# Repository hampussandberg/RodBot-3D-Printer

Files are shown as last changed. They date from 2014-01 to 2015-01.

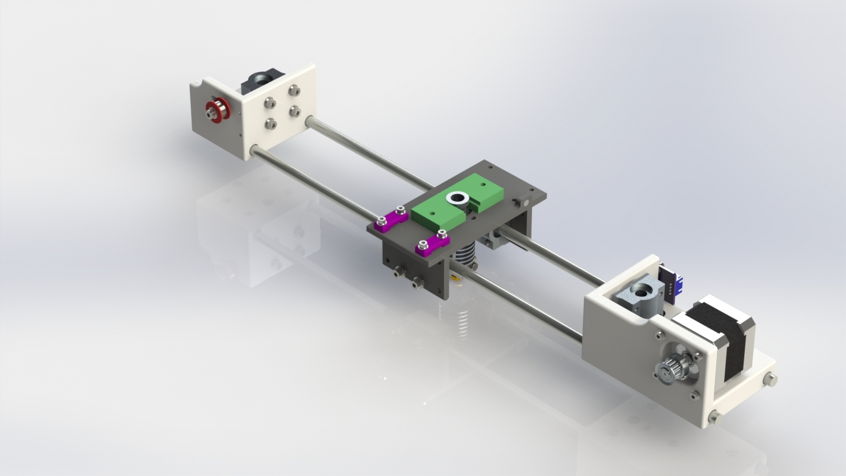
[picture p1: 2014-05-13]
Renderings - Images/X-Assembly Rev 2.JPG

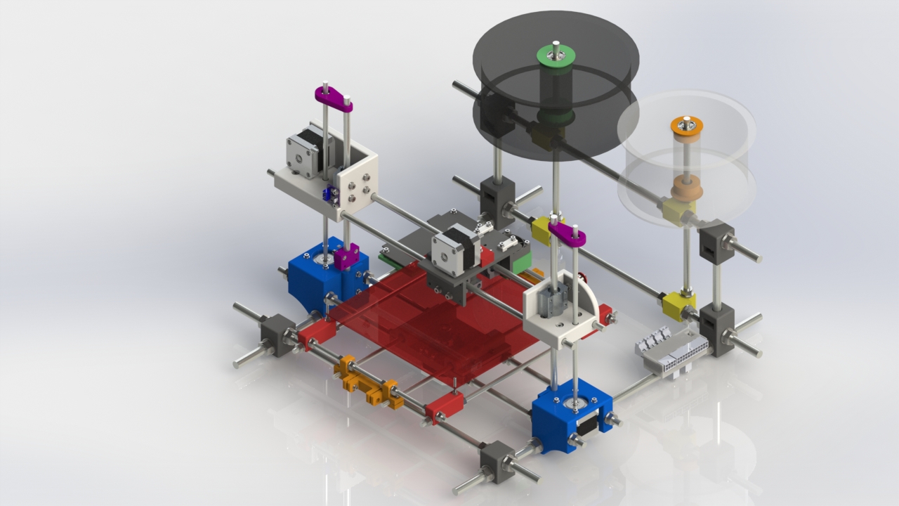
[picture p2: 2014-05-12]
Renderings - Images/Assembly.JPG

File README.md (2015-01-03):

##RodBot - 3D Printer  

This project started out as a small upgrade to a kit 3D printer I bought but ended up as a complete printer.  

It is designed around a frame of M10 threaded rods for stability, which is where the name come from as well. All plastic parts are printable and are made to be sturdy for stability.  

The weakest link I found in the kit printer I started out with was that many printed parts where mounted together to form a bigger part. I tried to avoid this by making the parts as big as necessary and only mounting hardware like rods and bearing blocks. This will of course mean more material is needed and the total weight of the printed parts is around 900 grams.  

The X-carriage was designed to fit a [Greg's Wade reloaded](http://www.thingiverse.com/thing:18379) or my remix of [Minimalistic Mk7 replacement](http://www.thingiverse.com/thing:251112)  
It's probably possible to use other extruders using the 50 mm hole distance as well.  

Some of the parts needed:  
* M10 threaded rods + nuts and washers  
* M8 threaded rods + nuts and washers  
* M6 threaded rods + nuts and washers  
* 8 mm Smooth rods  
* SC8UU bearing blocks  
* RepRap PCB Heatbed, I'm using [this one](http://reprap.me/heatbed/mk2-231.html)  

**Note:** Some parts might need to be rotated in order to print them.  

The frame blocks are designed to work with this [Heavy duty Vibration damper](http://www.thingiverse.com/thing:94279 )  

I have made a 3D PDF of the printer available for [download](https://github.com/hampussandberg/RodBot-3D-Printer/raw/master/Renderings%20-%20Images/RodBot%20Assembly%20Rev%203.PDF)  

##Updates:  
**2015-01-03:** Some changes have been made since the last update. The biggest are:  
- New heatbed: [Helios Heat Bed kit](http://www.panucatt.com/product_p/hbp200.htm)  
- New extruder: [Bulldog XL Extruder](http://www.reprapdiscount.com/mechanics/64-bulldog-xl-extruder.html)  
- Changed Z-axis threaded rods to [trapezoidal lead screw](http://www.ebay.com/itm/TR8x1-5Dx180mm-1-5mm-Pitch-Trapezoidal-Acme-Ballscrew-Leadscrew-Fine-Pitch-/221553098138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)  
- Adjustable belt tensioner for the X-axis  
All these changes has made the printer better and more importantly it seems like it's more reliable. All the new files are available on the [Github page](https://github.com/hampussandberg/RodBot-3D-Printer).  

**2014-05-30:** The Y-axis is now modified to use 8 mm smooth rods so that those are the only rods used for the whole printer and SC8UU are used everywhere. I also modifided the design of the Y-motor mount to be able to print it flat (prints faster) and tried to make it more robust. I recommend printing the Y-motor mount at 100% infill. The new parts are:  
- Y Motor Mount Rev 2  
- Y Smooth Rod Ends - Rev 2.1  
- Y Belt Holder Rev 2  

**2014-05-13:** The Marlin configuration I'm using with the RAMPS controller is available on [Github](https://github.com/hampussandberg/RodBot-Marlin-Ramps). I've also moved old compenent no longer used on the newest version of RodBot to an archive folder [here](https://github.com/hampussandberg/RodBot-3D-Printer/tree/master/Archive).    

**2014-05-12:** Modified the Y ends to have a easier and more robust clamp for the belt. It is now easier to adjust the tension as it's just a matter of turning to screws. This also removes the problem I had with the plastic holding the belt cracking. The new parts are:  
- Y Smooth Rod Ends - Rev 2  
- Y Belt Holder  
Hardware needed:  
- 2 pcs M3x25mm or longer  
- 2 pcs M3x16mm  
- 4 pcs M3 Lock nut  
- 2 pcs M3 nut  
- 8 pcs M3 washer  
Some photos of the assembly: [Photo 1](https://raw.githubusercontent.com/hampussandberg/RodBot/master/Renderings%20-%20Images/Photo%202014-05-12%2023%2004%2008.jpg), [Photo 2](https://raw.githubusercontent.com/hampussandberg/RodBot/master/Renderings%20-%20Images/Photo%202014-05-12%2023%2003%2046.jpg), [Photo 3](https://raw.githubusercontent.com/hampussandberg/RodBot/master/Renderings%20-%20Images/Photo%202014-05-12%2023%2003%2052.jpg).  

**2014-05-08:** All files are available on [GitHub](https://github.com/hampussandberg/RodBot-3D-Printer) along with some development and some old files as well.  

**2014-04-30:** I recently replaced my J-Head hotend with an [E3D hotend](http://e3d-online.com/) but I needed to widen the x assembly by 5 mm in order to fit it. The new parts for the wider x-assembly are:  
- X Carriage Rev 3  
- X-End Idler Clamp Rev 2  
- X-End Idler Rev 2  
- X-End Motor Clamp Rev 2  
- X-End Motor Rev 2  
To secure the E3D Hotend I'm using [this mount from dmarett](http://www.thingiverse.com/thing:220811). See the pictures I've taken for more details.

**2014-03-29:** The fan mount I designed didn't work very well so I have now replaced it with [this](http://www.thingiverse.com/thing:283862), which is a remix of [this one](http://www.thingiverse.com/thing:30721) but with a slightly modified mount to fit on the two screws for the belt holders.

##License
<br />This work is licensed under a <a rel="license" href="http://creativecommons.org/licenses/by-sa/4.0/">Creative Commons Attribution-ShareAlike 4.0 International License</a>.

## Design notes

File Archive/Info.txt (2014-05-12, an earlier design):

Upgraded version of Portabee

Some parts might need to be rotated so they are printed correctly.  

Works nicely with these vibration dampers http://www.thingiverse.com/thing:94279  

**UPDATE Dec 12 - 2013**  
Working on the x-assembly right now with a new extruder mount which hopefully will be more stable than the current one. I've also designed some new end stops based on A1301 hall sensors, just waiting for the PCB's to arrive so I can start using them. For the x-assembly I've been using SC8UU linear bearings found on eBay. They seem to be quite sturdy! I will update more once I receive some more bearings so that I can start assembling the x-assembly.  
I've exported a 3D-PDF available in the download section or here: http://www.thingiverse.com/download:377081  

**UPDATE Nov 13 - 2013**   
I have now printed and assembled a version which works. Some small changes has been made to make all the parts more robust so any real pictures of the machine might differ a bit from the STL-models. Works extremely well and feels very strong which was the main reason I started with this upgrade. As it stands now only the X-assembly is still the original from Portabee but I intend on upgrading it as well which will make the whole machine "new"!  

I have now uploaded all the new parts that I use. Additional hardware is required:  
- M6 threaded rods and 6mm smooth rods for Y-assembly + nuts and washers  
- M10 threaded rods for the main frame + nuts and washers  
- Mostly M3 hex screws of various length (10, 12, 16, + some more)  
- M8 threaded rods to mount the Y-assembly on  

Total build area is now 175x150x150mm (X Y Z).  
I will update with a complete list when I have more time!  

**UPDATE Oct 2 - 2013**  
After designing the frame i realized how unstable the printer was in it self so I started working on a new base which is part of the frame (the blue pieces in the rendering). I noticed the y-assembly had some cracks in the parts so I designed a new single-block version and I also replaced the standard heatbed with a reprap one to get a bigger build area. (Basically all parts under the red heatbed in the rendering)  

**NOTE:**  
I'm still designing the parts and haven't printed them yet but here are some features the upgraded printer will have:  
- Bigger build area (200x200)  
- More stable y-assembly  
- Hall sensor endstops using A1301 for easier adjustment  
- Variable width for other types of build platform. Change the length of the rods for your needs  
- M8 threaded rods for y-assembly instead of M6  
- Electronics holder with cover (green part on the left side in rendering)  
- Probably more stuff once I'm done with the above  

**Feedback and/or requests are gladly received!**  

Parts with name OLD_nnn are parts from the old design where the original printer parts were placed in a holder on the metal frame.

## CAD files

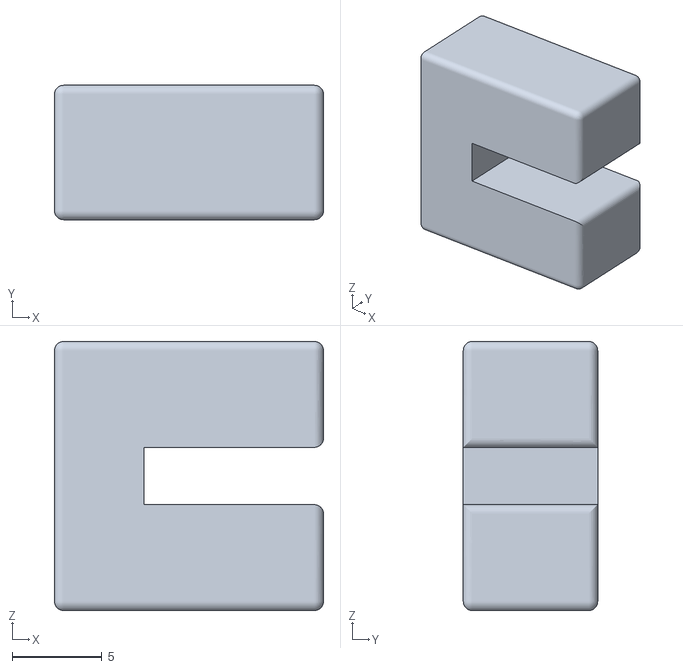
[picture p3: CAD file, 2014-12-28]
Accessories/Build Plate Holder/Clamp - 3.2mm.STL
15.0 x 7.50 x 15.0

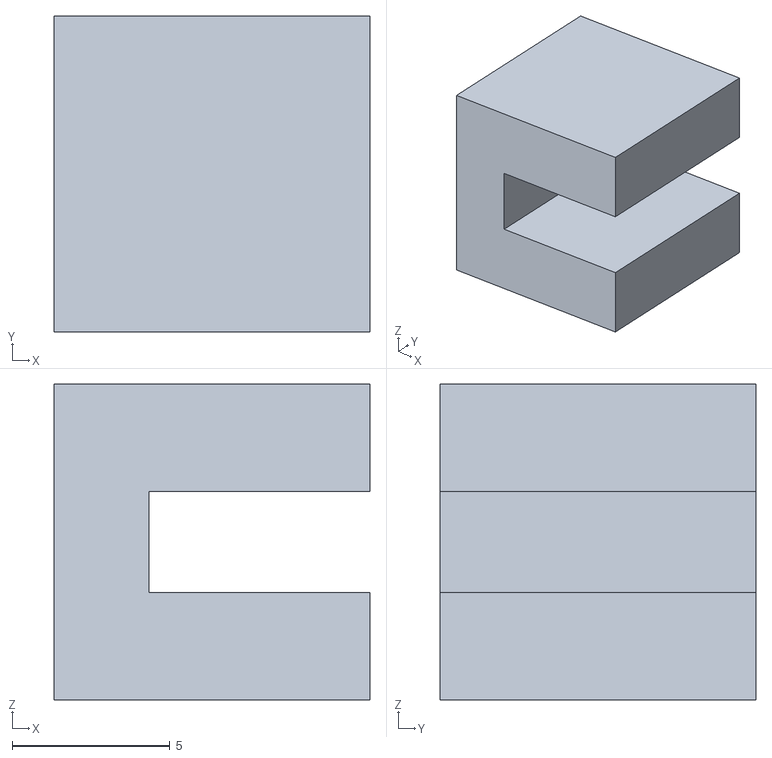
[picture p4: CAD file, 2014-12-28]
Accessories/Clamp.STL
10.0 x 10.0 x 10.0

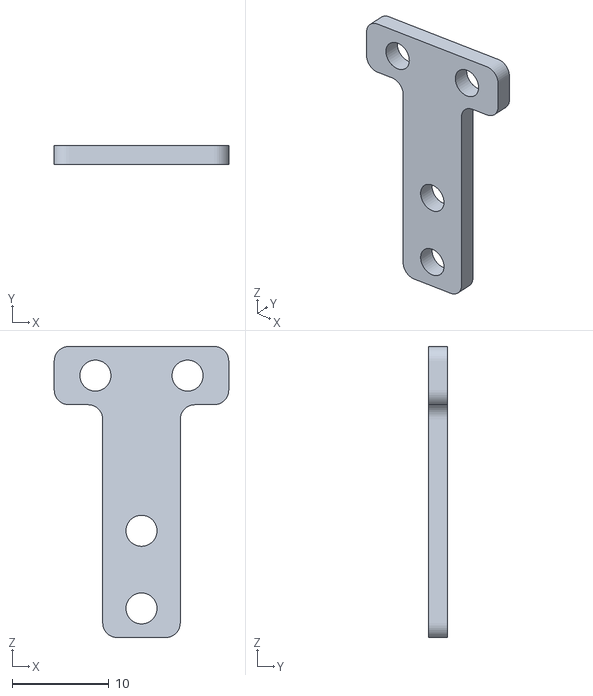
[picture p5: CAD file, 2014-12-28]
Accessories/Servo Holder/Switch Servo Horn Extension.STL
18.0 x 2.00 x 30.0

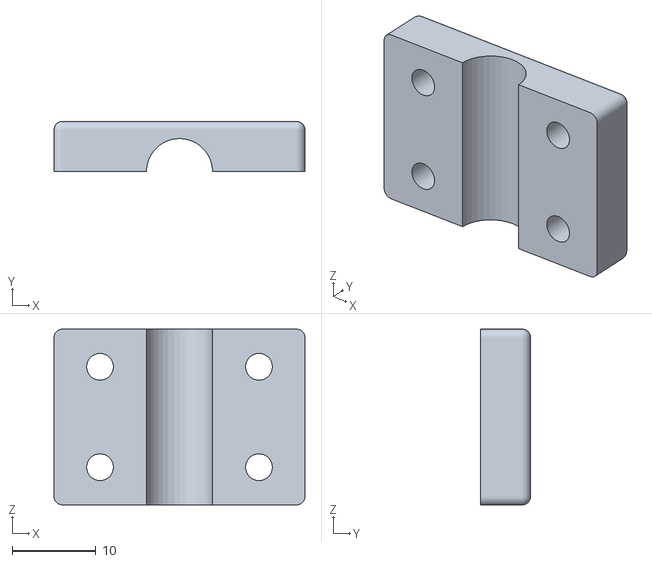
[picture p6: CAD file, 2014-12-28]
Z Endstop Holder.STL
30.0 x 6.00 x 21.0

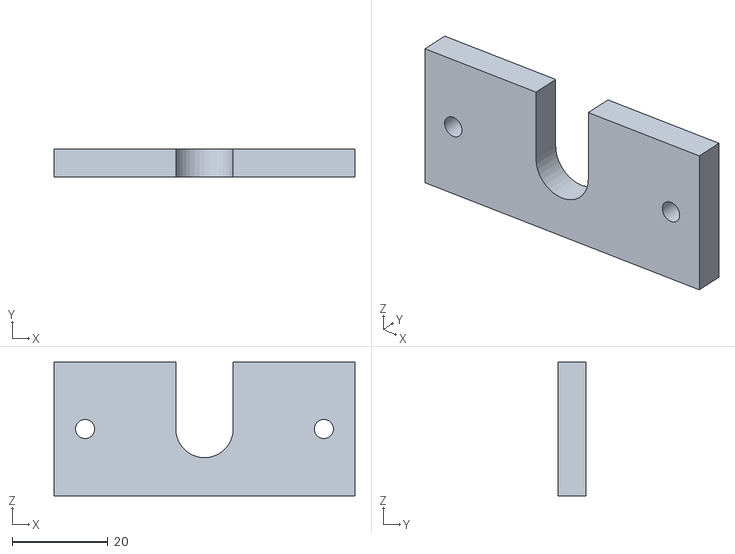
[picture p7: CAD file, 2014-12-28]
Accessories/E3D-v6 Mounting Plate.STL
63.0 x 5.80 x 28.0

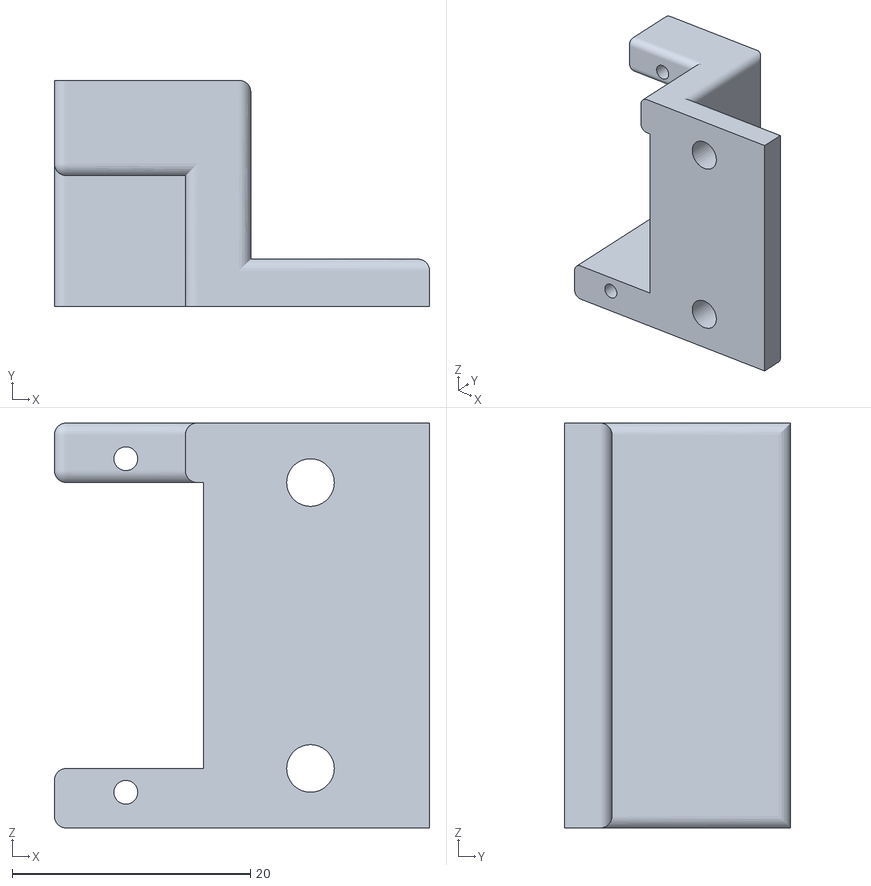
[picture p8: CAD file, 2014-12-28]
Accessories/Servo Holder/Servo Holder.STL
31.5 x 19.0 x 34.0

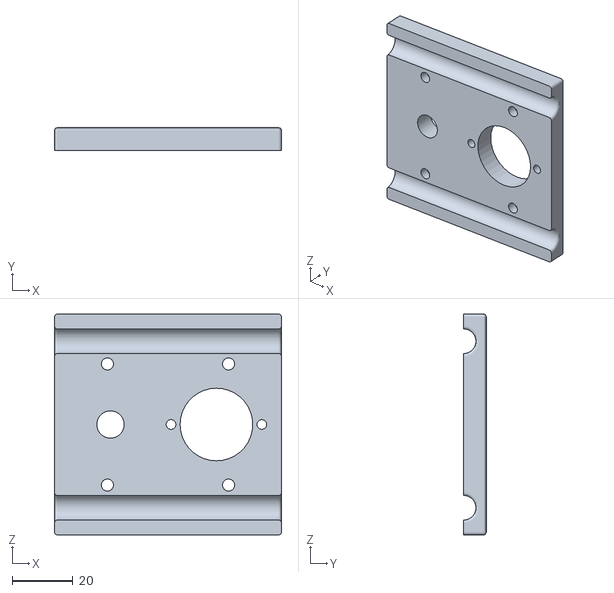
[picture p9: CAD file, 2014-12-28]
Development/X-End Idler Clamp Rev 3.STL
75.0 x 7.50 x 73.0

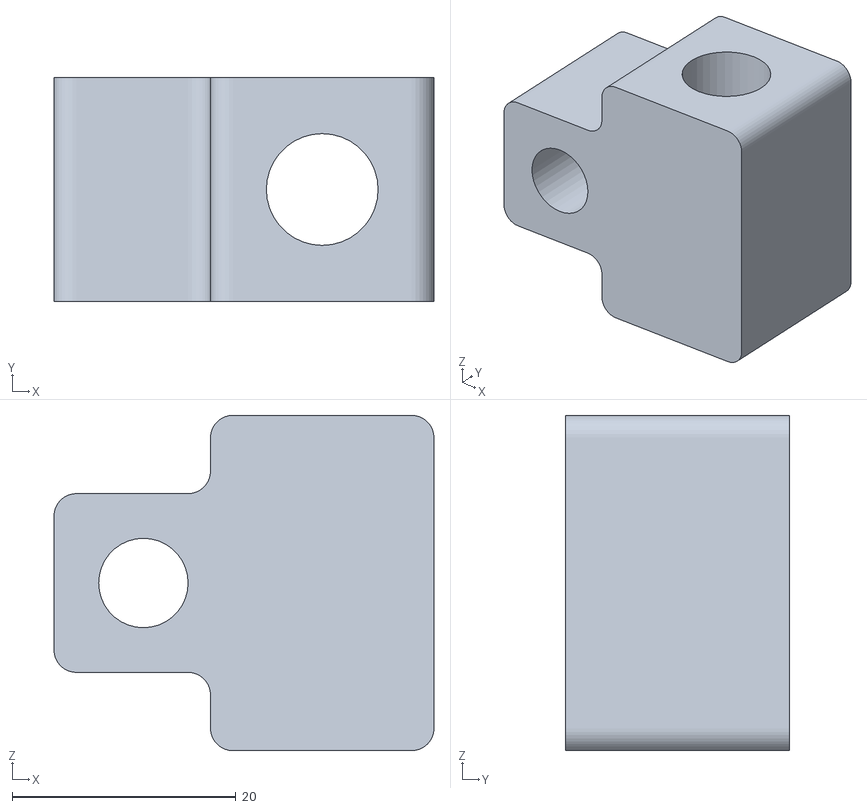
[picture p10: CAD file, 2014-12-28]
Filament Holder.STL
34.0 x 20.0 x 30.0

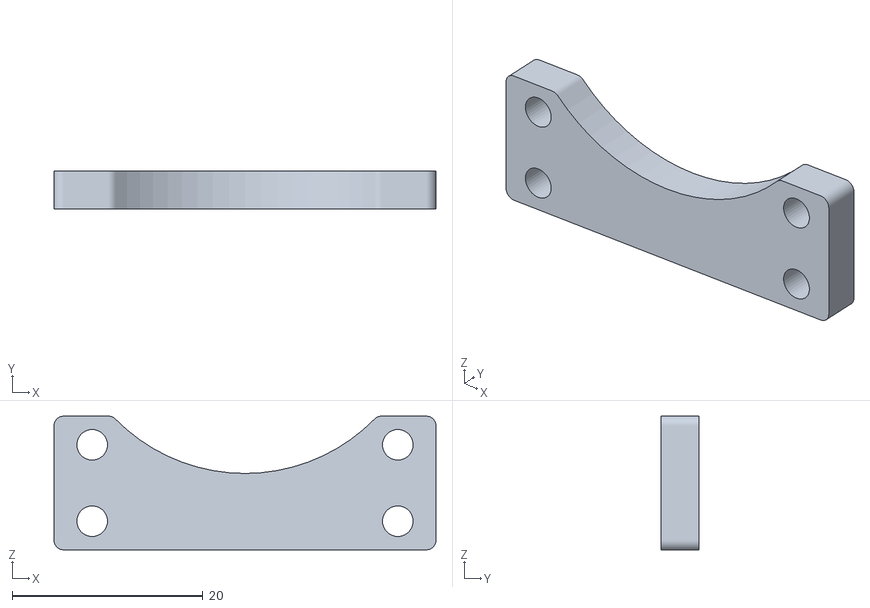
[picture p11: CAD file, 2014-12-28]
40mm Fan Mount.STL
40.0 x 4.00 x 14.0

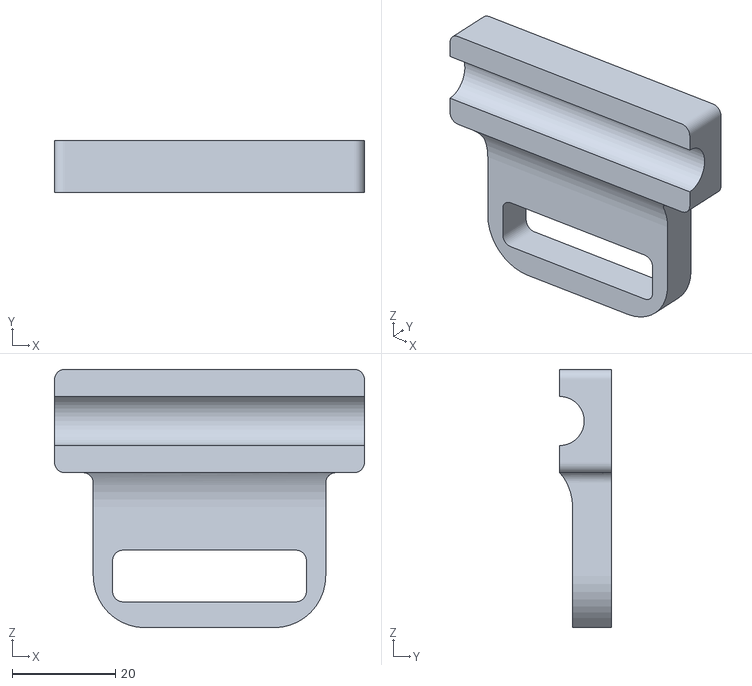
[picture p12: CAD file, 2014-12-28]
Accessories/Camera Mount.STL
60.0 x 10.00 x 50.0

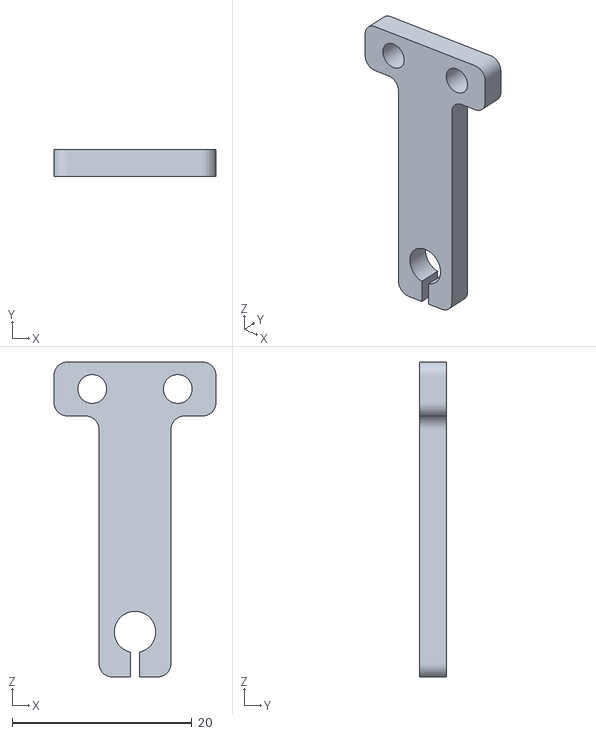
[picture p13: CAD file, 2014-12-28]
Accessories/Servo Holder/Servo Arm.STL
18.0 x 3.00 x 35.0

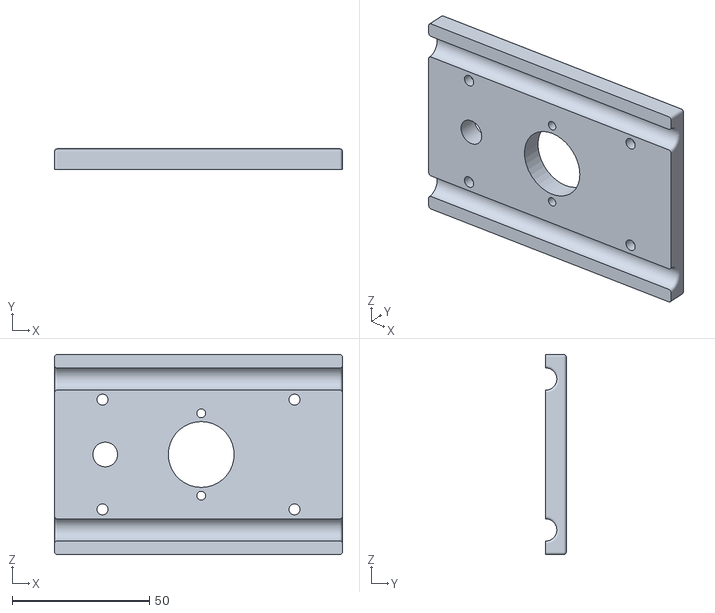
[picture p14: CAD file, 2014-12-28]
Development/X-End Motor Clamp Rev 3.STL
105.0 x 7.50 x 73.0

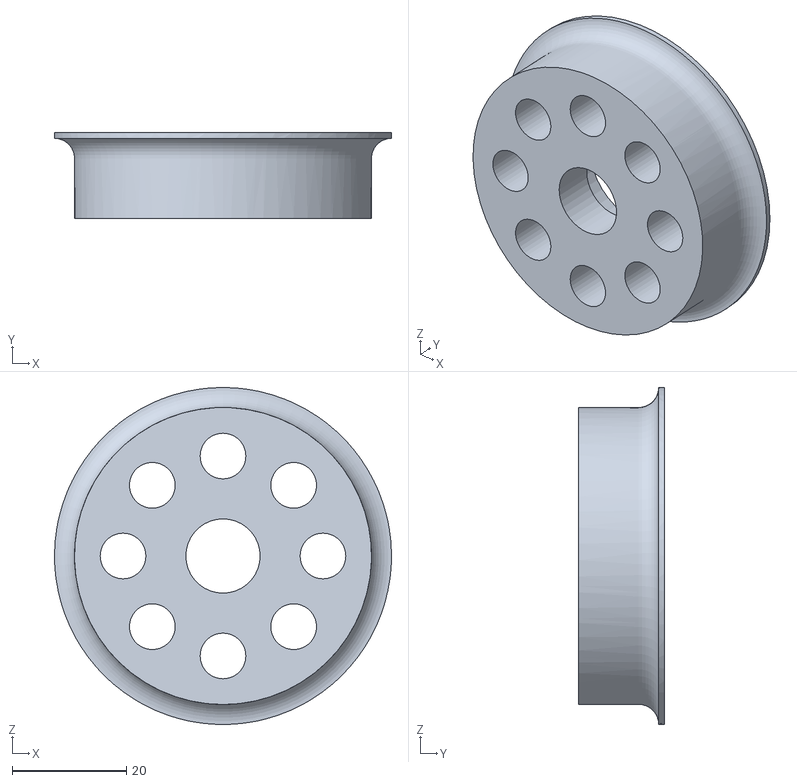
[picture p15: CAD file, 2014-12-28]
Accessories/Filament Spool Bearing Holder -ColorFabb.STL
59.0 x 15.0 x 59.0

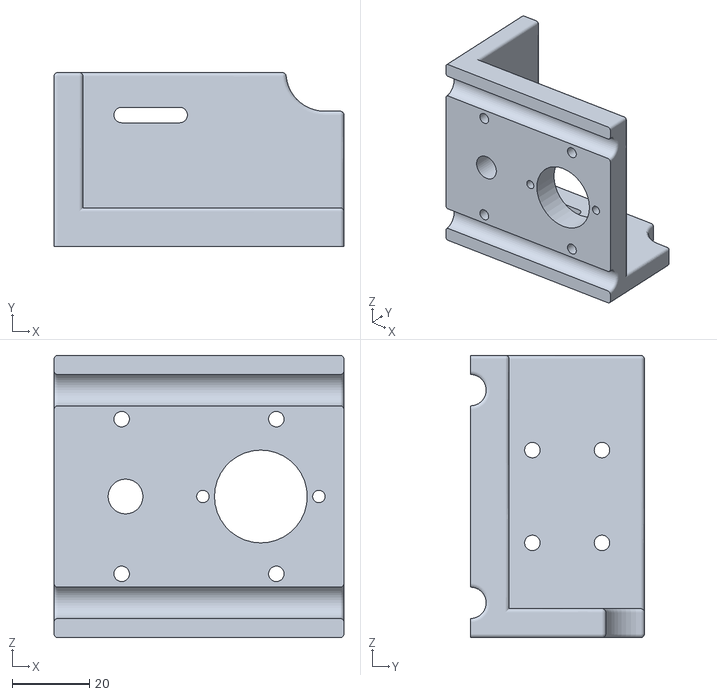
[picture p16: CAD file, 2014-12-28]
Development/X-End Idler Rev 3.STL
75.0 x 45.0 x 73.0

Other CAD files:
Accessories/RAMPS LCD Case.STL
Development/X-End Motor Rev 3.STL
Frame Small Block.STL
Accessories/10mm Mounting Bracket.STL
Accessories/ATX Power Supply Holder.STL
Accessories/ATX Power Supply Switch Board Holder.STL
Accessories/ATX Power Supply Switch Board Top.STL
Accessories/E3D Mounting Plate.STL
Accessories/Electronics Holder Base.STL
Accessories/Fan Mount Plug.STL
Accessories/Fan Mount.STL
Accessories/Filament Spool Bearing Holder - Big .STL
Accessories/Filament Spool Bearing Holder - Small.STL
Accessories/Y Camera Mount.STL
Accessories/Z Rods Stabilizer.STL
Archive/Base Upgrade.STL
Archive/Bearingholder.STL
Archive/Direct Extruder Spacer.STL
Archive/Electronics Holder Base.STL
Archive/Electronics Holder Cover.STL
Archive/Filament Guide.STL
Archive/Frame Back Block - With Support.STL
Archive/Frame Front Block - With Support.STL
Archive/Frame Small Block - With Support.STL
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

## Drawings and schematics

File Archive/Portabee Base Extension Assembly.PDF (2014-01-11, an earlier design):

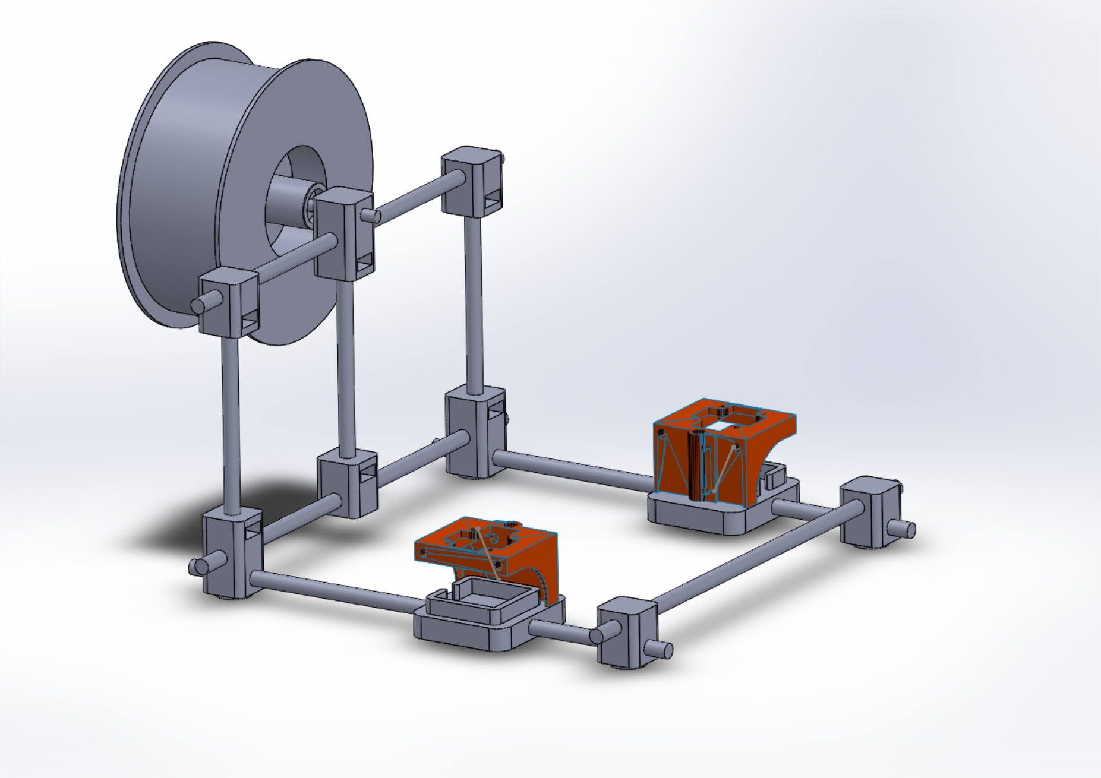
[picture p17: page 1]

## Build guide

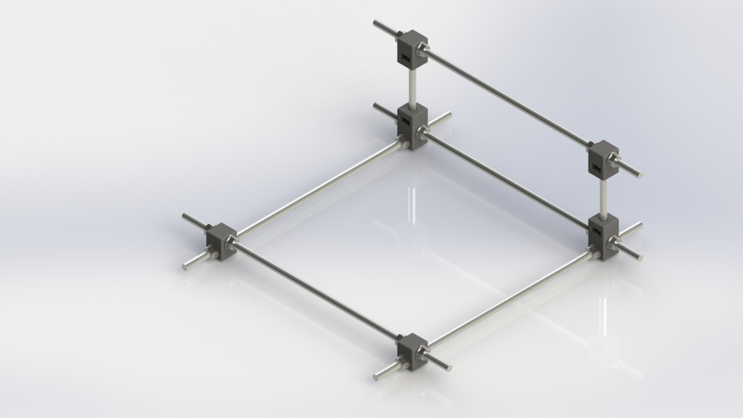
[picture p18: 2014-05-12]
Renderings - Images/Frame-Assembly.JPG

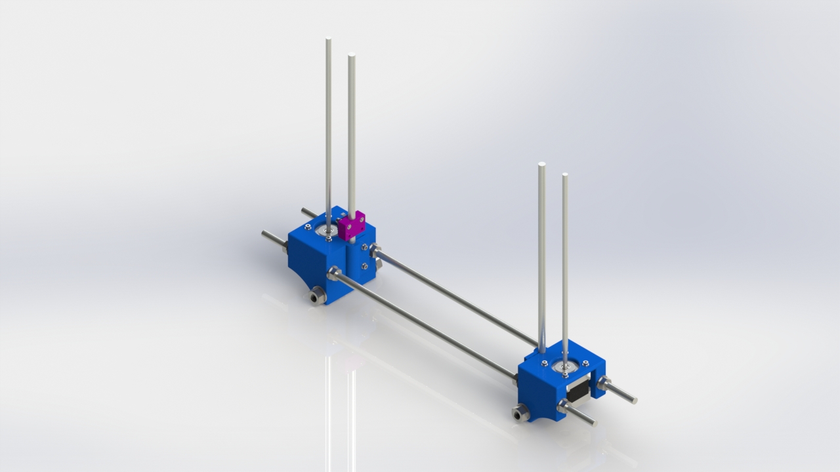
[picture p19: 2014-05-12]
Renderings - Images/Base Blocks-Assembly.JPG

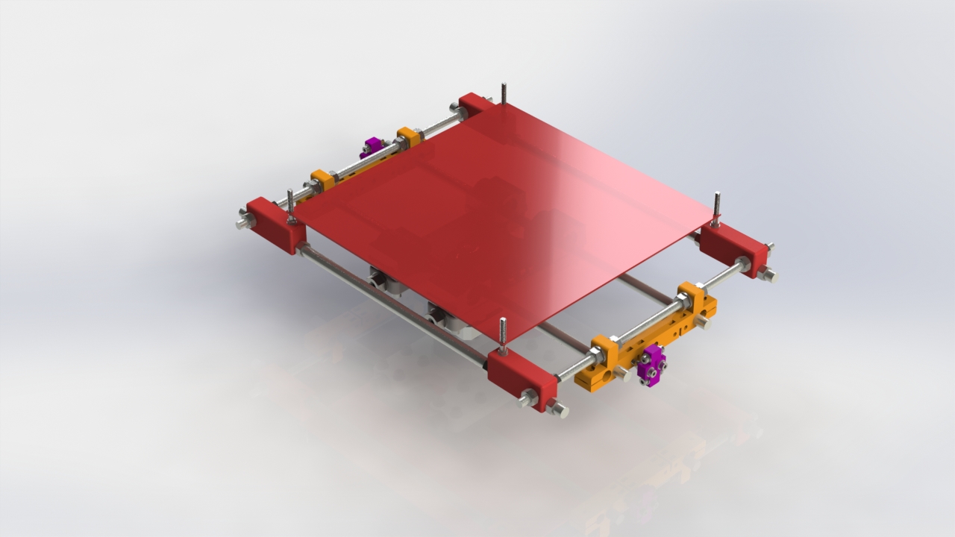
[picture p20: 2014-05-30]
Renderings - Images/Y Assembly Rev 2.JPG

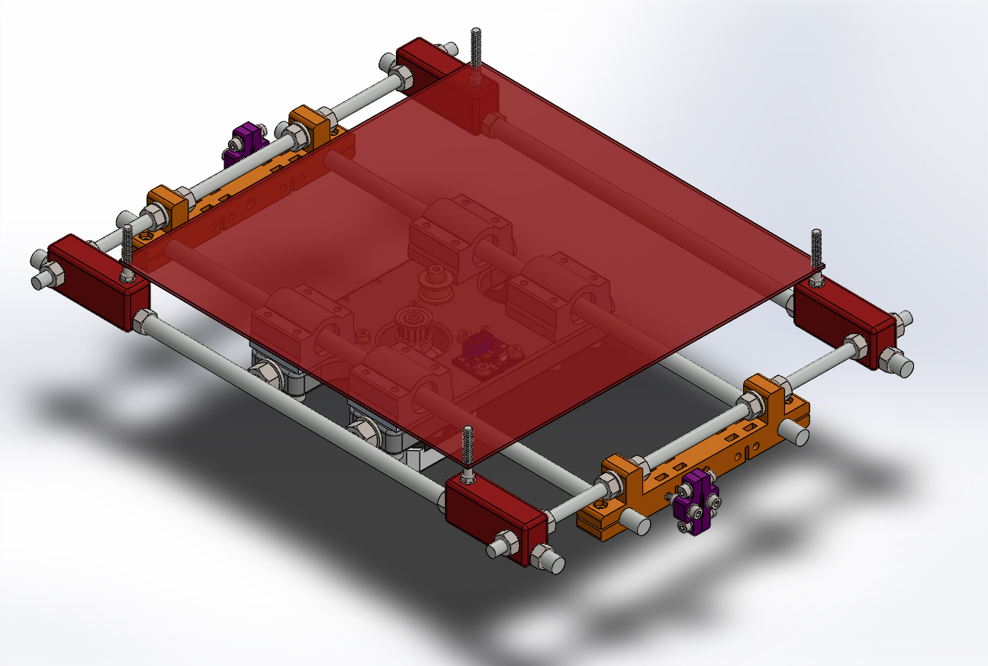
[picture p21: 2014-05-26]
Development/8mm Y-Axis/Y Assembly Rev 2.JPG

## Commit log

2014-01-19 Continued work on X assembly and started printing it as well
    [10mm Mounting Bracket.STL, ATX Power Supply Holder.STL, ATX Power Supply Switch Board Holder.STL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]
2014-05-08 Updated X-carriage and many more things
    [Black Filament Spool Bearing Holder.STL, Black Small Filament Spool Bearing Holder.STL, Direct Extruder Spacer.STL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]
2014-05-09 Added mounting plate for E3D Hot End
    [E3D Mounting Plate.STL]
2014-05-11 Decreased the length of the E3D Mount to be easier to assemble
    [E3D Mounting Plate.STL]
2014-05-12 New Y Ends
    [Dual Extruder Connection Plate.STL, E3D Mounting Plate.STL, Y Belt Holder.STL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]
2014-05-13 Added new renderings and reorganized some files
    [J-Head Mounting Bracket - Mirrored.STL, J-Head Mounting Bracket - Portabee Hot End.STL, J-Head Mounting Bracket.STL]
2014-05-22 Added dev files for quad z-axis
    [Base Block Quad Mirrored.STL, Base Block Quad.STL, X-End Idler Clamp Rev 2 Quad.STL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]
2014-05-22 Added README for quad z-axis
2014-05-22 Updated README for quad z-axis
2014-05-26 Added files for 8mm Y-axis upgrade
    [Washer M4 2.4mm.STL, Y Belt Holder.STL, Y Motor Mount Rev 2.STL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]
2014-05-26 Added some images for the new Y-axis
2014-05-30 Updated with new 8 mm Y-axis
    [Washer M4 2.4mm.STL, Y Belt Holder Rev 2.STL, Y Belt Holder.STL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]
2014-06-03 Moved Quad Z-axis to a separate repository
    [Base Block Quad Mirrored.STL, Base Block Quad.STL, X-End Idler Clamp Rev 2 Quad.STL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]
2014-06-15 Added Y Smooth Rod Ends with higher tab
    [Y Smooth Rod Ends - Rev 2.1 - Higher Tab.STL]
2014-06-15 New X-carriage with 3 bearings instead of 2
    [X Carriage Rev 3.1.STL]
